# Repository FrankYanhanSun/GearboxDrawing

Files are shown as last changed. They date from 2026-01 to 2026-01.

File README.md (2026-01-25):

# 机械设计课程作业-减速箱

本仓库提供一个开源的机械设计课程作业可供参考。适用于全国广大高等院校机械专业的机械设计课程。需注意：**本仓库设计内容为二级展开式齿轮减速器（斜齿）**，传动简图：

<div align="center">
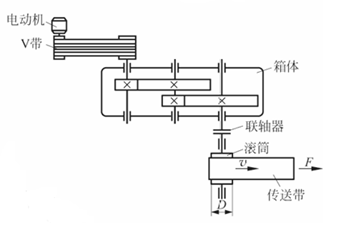
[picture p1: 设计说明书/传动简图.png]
    
</div>

## 初始参数

<div align="center">

| 运输带工作拉力 $F$ | 运输带工作速度 $v$ | 滚筒直径 $D$ | 滚筒效率 $\eta_w$ | 
| --- | --- | --- | --- |
| 5250N | 0.85m/s | 410mm | 0.96 |

</div>

- 两班制，连续单向运转，载荷平稳；要求传动使用寿命为 10 年。

---

## 设计说明书

请见`设计说明书`文件夹，可直接导入`overleaf`进行编辑，需将`Latex`   编译器更改为`XeLaTeX`进行编译。

---

## 图纸

`装配图.dwg`：
<div align="center">
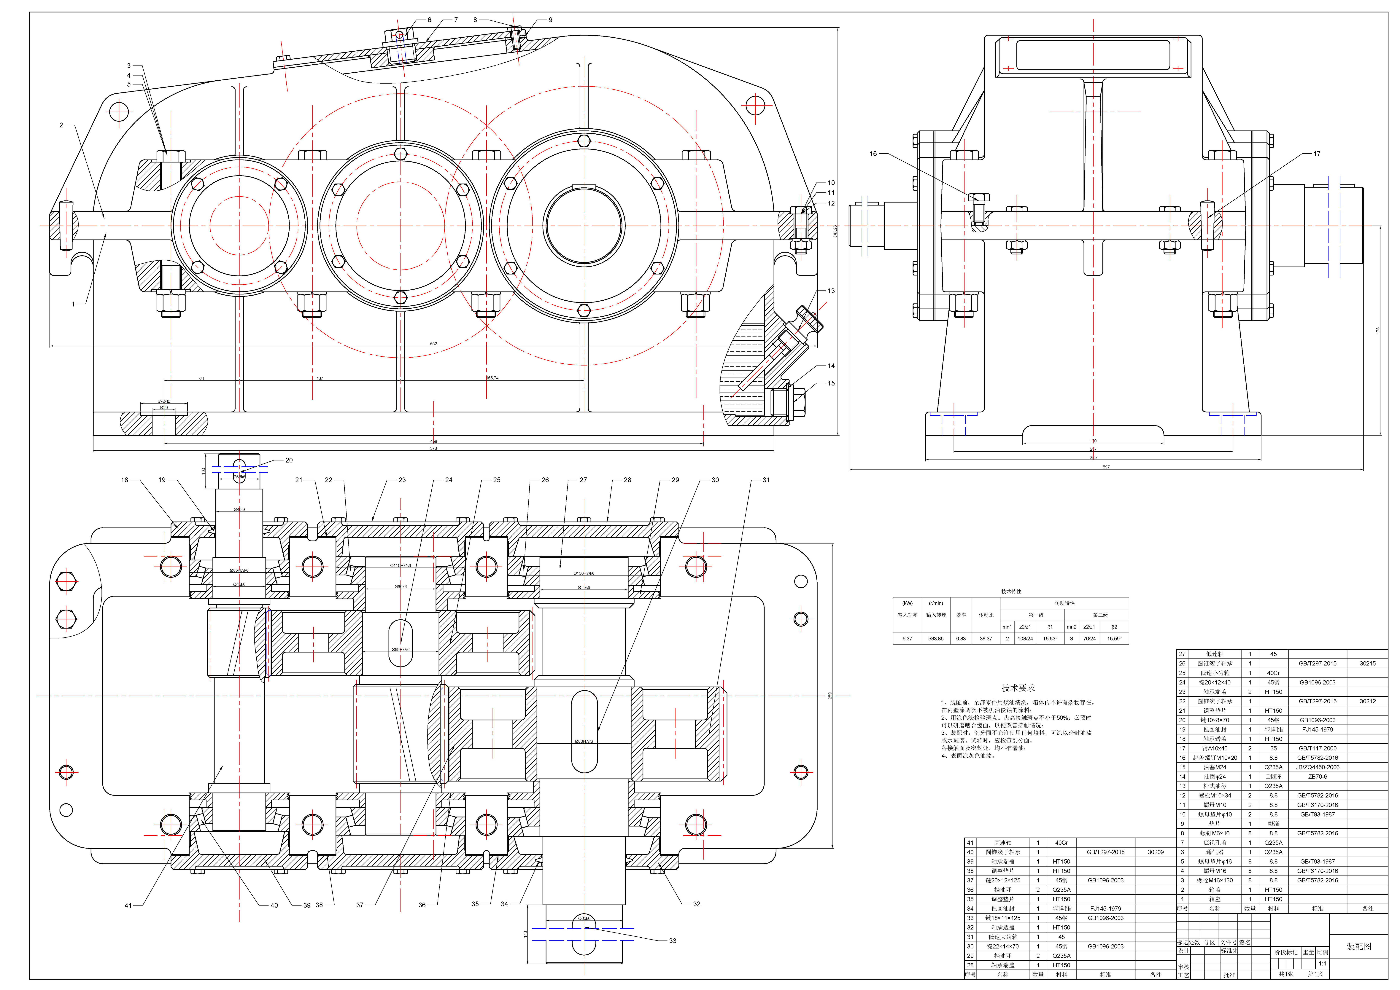
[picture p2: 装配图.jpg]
    
</div>

`零件图(中间轴).dwg`：
<div align="center">
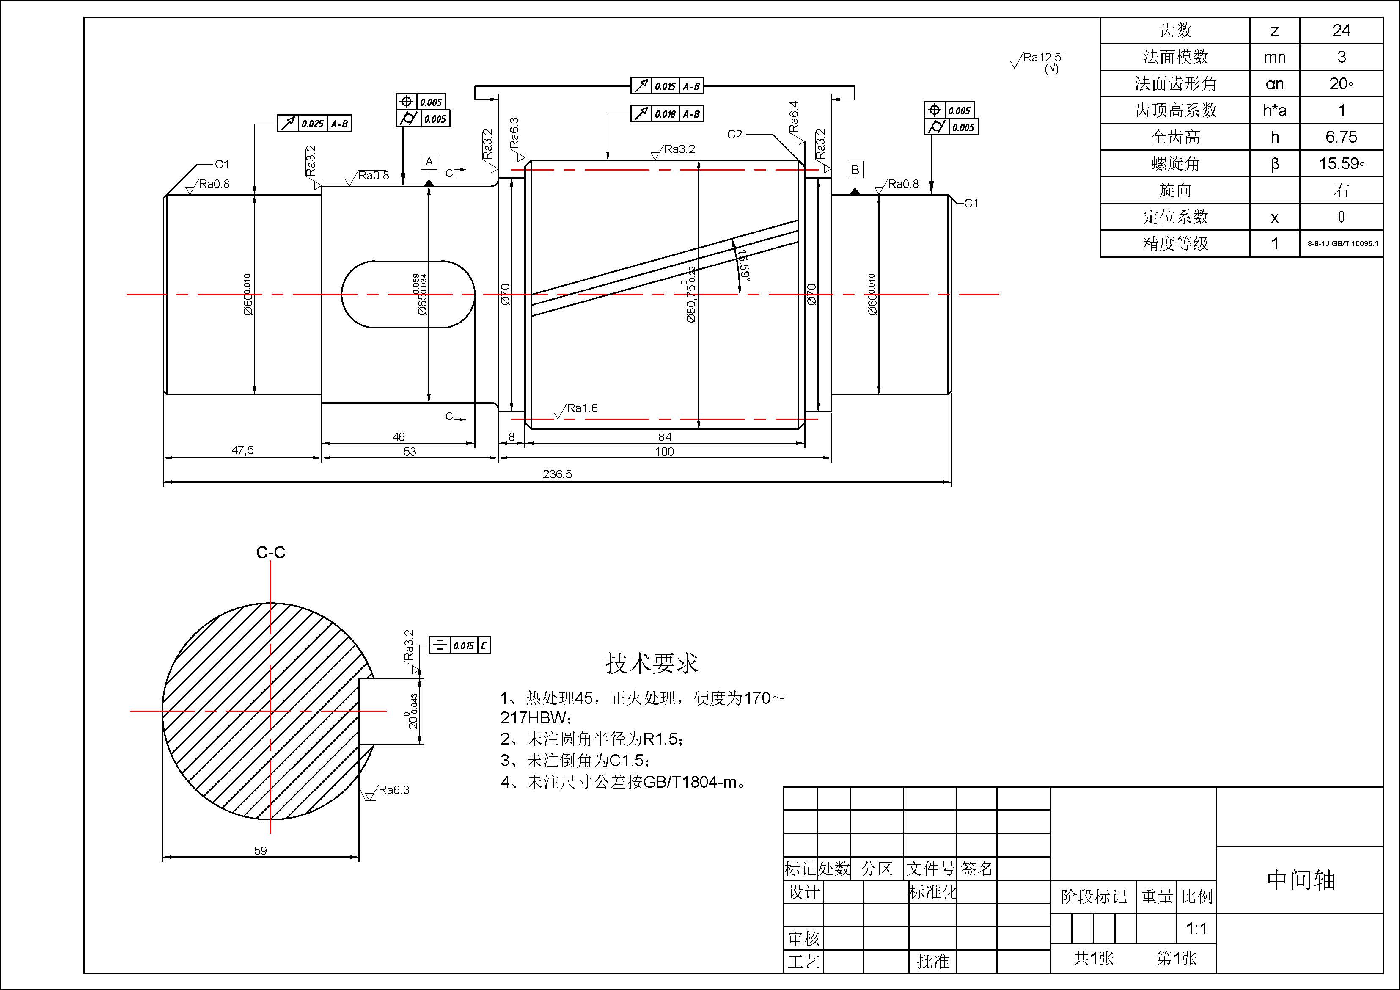
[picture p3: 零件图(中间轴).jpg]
    
</div>

---

## Acknowledgement

感谢b站up主天上一白的视频[机械设计课程设计/减速器设计—全流程详解](https://www.bilibili.com/video/BV1A44y197Hb/?vd_source=a416fcb6c88258170a1902d8753f0269)，帮助我完成了学校老师什么也没讲就布置的作业。看到本仓库的同学也可以去跟着学习一下。

参考书目：
- [《机械设计教程——理论、方法与标准（第2版）》-清华大学出版社](https://detail.tmall.com/item.htm?id=743610688816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)<br>巨烂，计算部分全是错的，但是是我们学校老师编的教材，不得不用
- [《机械设计课程设计（第6版）》-机械工业出版社](https://item.taobao.com/item.htm?id=691022636697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)<br>推荐将本书作为课程设计的参考，流程、标准都很详细

---

$^*$ 所有内容仅供参考，部分内容有错请详细辨认。

---

## Leave a star if you like it 🥰

<br>Star History Chart (https://www.star-history.com/#FrankYanhanSun/GearboxDrawing&Date)
<br>

© 2025 Yanhan Sun (Frank).

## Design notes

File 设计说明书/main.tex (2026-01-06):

\documentclass{article}
\usepackage{geometry}

\geometry{letterpaper,left=2cm,right=2cm,top=3cm,bottom=2cm}
\usepackage{ctex}
\usepackage[english]{babel}
% \usepackage[english]{babel}
\usepackage{amsthm}
\usepackage{amssymb}
\newtheorem{theorem}{Theorem}
\newtheorem{corollary}{Corollary}
\newtheorem{lemma}{Lemma}
\usepackage{amsmath}
\usepackage{graphicx}
\usepackage{multirow}
\usepackage{ulem}
\usepackage{setspace}
\newcommand{\ulinecontent}[2]{\underline{\makebox[#1][c]{#2}}}

\begin{document}
\renewcommand\qedsymbol{$\blacksquare$}

\begin{titlepage}
    \centering
    \onehalfspacing % 1.5倍行距

    % ----------------------------------------------------
    % 顶部：学校名称
    % ----------------------------------------------------
    \vspace*{0.5cm}
    
    % 使用 \zihao{1} 设置一号字 (约26pt)
    % 这里的 \cdot 是中间的点，也可以直接用中文输入法打出
    {\zihao{1} \heiti * \ \ * \ \ 大 \ \ 学}
    
    \vspace{2cm}

    % ----------------------------------------------------
    % 标题：机械设计项目计算说明书
    % ----------------------------------------------------
    % 使用 \zihao{-0} 设置小初号字 (约36pt)
    {\zihao{-0} \heiti 机械设计项目计算说明书}

    \vspace{3cm}

    % ----------------------------------------------------
    % 中间信息栏
    % ----------------------------------------------------
    % 使用表格来对齐标签和下划线
    % l 为左对齐(或居中)，r 为右对齐
    
    {\zihao{3} \songti % 设置字号为三号
        \renewcommand{\arraystretch}{2.0} % 增加表格行高
        
        \begin{tabular}{r @{：} l}
            % \makebox[4.5em][s]{...} 用于强制文字两端对齐(分散对齐)
            
            \textbf{题目 (中文)} & \ulinecontent{260pt}{二级展开式齿轮减速器结构设计} \\
            
            \textbf{\makebox[4.5em][s]{姓名}} & \ulinecontent{260pt}{***} \\
            
            \textbf{\makebox[4.5em][s]{学号}} & \ulinecontent{260pt}{***} \\
            
            \textbf{院 \quad (系)} & \ulinecontent{260pt}{***} \\
            
            \textbf{\makebox[4.5em][s]{专业}} & \ulinecontent{260pt}{***} \\
            
            \textbf{指导教师} & \ulinecontent{260pt}{***} \\
        \end{tabular}
    }

    \vfill % 自动填充垂直空间，把日期推到底部

    % ----------------------------------------------------
    % 底部：日期
    % ----------------------------------------------------
    {\zihao{3} \songti 二〇**年 * 月}
    
    \vspace{2cm}

\end{titlepage}

\newpage
\tableofcontents

\newpage
\section{传动方案}
\subsection{已确定方案：设计带式运输机的展开式二级圆柱齿轮减速器}

\subsection{传动简图}
\begin{figure}[h!]
    \centering
    
    \caption{带式运输机的展开式二级圆柱齿轮减速器的传动简图}
    \label{fig:传动简图}
\end{figure}

\subsection{已知}

（1）运输带工作拉力$F = 5250 \text{N}$；

（2）运输带工作速度 $v = 0.85 \text{m/s}$ (运输带速度允许误差$±5\%$)；

（3）滚筒直径$D = 410 \text{mm}$；

（4）滚筒效率$\eta_w = 0.96$（包括滚筒与轴承的效率损失）；

（5）工作情况: 两班制，连续单向运转，载荷平稳；

（6）要求传动使用寿命为10年。

%提示：请参考“机械设计教程”第1章1.4节，需给出电动机主要参数表、电动机安装及有关尺寸主要参数表、各轴的运动和动力参数表。

\section{电动机的选择}
\subsection{确定电动机功率}
工作主轴所需功率 $P_w$：
\begin{equation}
    P_w = \frac{Fv}{1000} = P_w = \frac{5250 \times 0.85}{1000} = 4.46 \text{kW}
\end{equation}

图片\ref{fig:传动简图}中传动装置包括：V带、三对滚动轴承、两对圆柱齿轮、一个联轴器，总效率为 $\eta = \eta_{\text{V带}} \times \eta_{\text{滚动轴承}}^3 \times \eta_{\text{圆柱齿轮}}^2 \times \eta_{\text{联轴器}} \times \eta_w$。根据表1.3，$\eta_{\text{V带}} = 0.95, \eta_{\text{滚动轴承}} = 0.98, \eta_{\text{圆柱齿轮}} = 0.98, \eta_{\text{联轴器}} = 0.99$。可以得到：
\begin{equation}
    \eta = \eta_{\text{V带}} \times \eta_{\text{滚动轴承}}^3 \times \eta_{\text{圆柱齿轮}}^2 \times \eta_{\text{联轴器}} \times \eta_w = 0.95 \times 0.98^3 \times 0.98^2 \times 0.99 \times 0.96 = 0.83
\end{equation}

电动机所需功率$P_d$:
\begin{equation}
    P_d = \frac{P_w}{\eta} = \frac{4.46}{0.83} = 5.37 \text{kW}
\end{equation}

考虑到在各零部件设计时需要有一定的工况系数，取电动机的工况系数为1.3，则电动机的额定功率$P_{ed}$：
\begin{equation}
    P_{ed} \ge  k_A P_d = 1.3 \times 5.37 = 6.98 \text{kW}
\end{equation}
根据附表K.1，选取电动机额定功率$P_{ed} = 7.5 \text{kW}$

\subsection{确定电动机转速}
工作机主轴转速 $n_w$：
\begin{equation}
    n_w = \frac{60 \times 1000 \times v}{\pi D} = \frac{60 \times 1000 \times 0.85}{\pi \times 410} = 39.59 \text{r/min}
\end{equation}

根据工作机主轴转速 $n_w$ 及有关机械传动的常用传动比范围(见表 1.2), 取普通 V 带的传动比 $i_带 = 2\textasciitilde{}4$, 二级圆柱齿轮传动比 $i_1 = i_2 = 3\textasciitilde{}6$, 可计算电动机转速的合理范围为 $n_d = n_w i_1 i_2 i_3 = 39.59 \times (2\textasciitilde{}4) \times (3\textasciitilde{}6) \times (3\textasciitilde{}6) \text{r/min} = 712.62\textasciitilde{}5700.96 \text{r/min}$。

根据附表 K.1, 符合这一范围的电动机同步转速有 $750 \text{r/min}$、1000 \text{r/min}$、1500 \text{r/min}$ 和 $3000 \text{r/min}$ 4 种, 现选用同步转速 $1500 \text{r/min}$, 满载转速 $n_m = 1440 \text{ r/min}$ 的电动机, 查得其主要参数和安装尺寸如表\ref{tab:电动机主要参数}和表\ref{tab:电动机安装及有关尺寸主要参数}所示。

\begin{table}[h]
\centering
\caption{电动机主要参数}
\label{tab:电动机主要参数}
\begin{tabular}{|c|c|c|c|c|c|}
\hline
型号 & 额定功率 & 同步转速 & 满载转速 & 堵转转矩/额定转矩 & 最大转矩/额定转矩 \\
\hline
Y132M-4 & 7.5kW & 1500r/min & 1440r/min & 2.2 & 2.2 \\
\hline
\end{tabular}
\end{table}

\begin{table}[h]
\centering
\caption{电动机安装及有关尺寸主要参数 \ \ mm}
\label{tab:电动机安装及有关尺寸主要参数}
\begin{tabular}{|c|c|c|c|c|c|}
\hline
\multirow{2}{*}{中心高} & 外形尺寸 & 地脚安装 & 地脚螺栓 & 轴伸尺寸 & 键公称尺寸 \\
 & $L \times (AC/2 + AD) \times HD$ & 尺寸 $A \times B$ & 直径 $K$ & $D \times E$ & $F \times h$ \\
\hline
132 & $515 \times 345 \times 315$ & $216 \times 178$ & 12 & $38 \times 80$ & $10 \times 8$ \\
\hline
\end{tabular}
\end{table}

\subsection{传动装置总传动比的计算及各级传动比的分配}
传动装置总传动比$i$:
\begin{equation}
    i = \frac{n_m}{n_w} = \frac{1440}{39.59} = 36.37
\end{equation}
取$i_{\text{V带}} = 2.6$， 那么$i_1 i_2 = i / i_{\text{V带}} = 13.98$，查表1.7得：一级齿轮传动比$i_1 = 4.5$，二级齿轮传动比$i_2 = 3.15$，误差为$e = |3.15 \times 4.5 \times 2.6 - 36.37| / 36.37 = 1.3\% $，误差控制在$±(3\textasciitilde{}5)\%$以内。

\subsection{传动装置运动和动力参数计算}

\subsubsection{计算各轴输入功率}
v带轴功率 $P_d = 5.37 \text{ kW}$

齿轮轴I功率 $P_I = P_d \eta_{\text{v带}} = 5.37 \times 0.95 \text{ kW} = 5.10 \text{ kW}$

齿轮轴II功率 $P_{II} = P_I \eta_{\text{滚动轴承}} \eta_{\text{圆柱齿轮}} = 5.10 \times 0.98^2 \text{ kW} = 4.90 \text{ kW}$

齿轮轴III功率 $P_{III} = P_{II} \eta_{\text{滚动轴承}} \eta_{\text{圆柱齿轮}} = 4.90 \times 0.98^2 \text{ kW} = 4.71 \text{ kW}$

\subsubsection{计算各轴转速}
v带轴转速 $n_d = n_m = 1440 \text{ r/min}$

齿轮轴I转速 $n_I = \frac{n_d}{i_{\text{v带}}} = \frac{1440}{2.6} = 553.85 \text{ r/min}$

齿轮轴II转速 $n_{II} = \frac{n_I}{i_1} = \frac{553.85}{4.5} = 123.08 \text{ r/min}$

齿轮轴III转速 $n_{III} = \frac{n_{II}}{i_2} = \frac{123.08}{3.15} = 39.07 \text{ r/min}$

\subsubsection{计算各轴转矩}
v带轴转矩 $T_d = 9550\frac{P_d}{n_d} = 9550 \times \frac{5.37}{1440} = 35.61 \text{ N} \cdot \text{m}$

齿轮轴I转矩 $T_I = 9550\frac{P_I}{n_I} = 9550 \times \frac{5.1015}{553.85} = 87.97 \text{ N} \cdot \text{m}$

齿轮轴II转矩 $T_{II} = 9550\frac{P_{II}}{n_{II}} = 9550 \times \frac{4.8995}{123.08} = 380.17 \text{ N} \cdot \text{m}$

齿轮轴III转矩 $T_{III} = 9550\frac{P_{III}}{n_{III}} = 9550 \times \frac{4.7055}{39.07} = 1150.14 \text{ N} \cdot \text{m}$

\section{带传动设计}

\subsection{已知}
（1）电动机功率$P=5.37kW$

（2）电动机转速$n_{1}=1440r/min$

（3）减速箱高速轴转速$n_{2}=553.85r/min$

\subsection{功率计算}
根据载荷性质和每天运转时间, 根据表5.6确定工作情况系数 $K_{A}=1.2$
\begin{equation}
P_{ca}=K_{A}P_{d}=1.2\times5.37=6.44(kW)
\end{equation}

\subsection{带型选择}
根据 $P_{ca}$ 与 $n_{d}$, 由图5.8确定选用B型普通V带。

\subsection{确定带轮基准直径}
由表5.2取小带轮基准直径 $D_{1}=132mm$。 根据式(5.24), 计算从动轮基准直径 $D_{2}$
\begin{equation}
D_{2}=iD_{1}=2.6\times132=343.2(mm)
\end{equation}
根据表5.4, 取 $D_{2}=355~mm$。
按式(5.23)验算带的速度
\begin{equation}
v=\frac{\pi D_{1}n_{1}}{60\times1000}=\frac{\pi\times132\times1440}{60\times1000}=9.95(m/s)<30(m/s)
\end{equation}
带的速度合适。

\subsection{确定V带的基准长度和传动中心距}
根据 $0.7(D_{1}+D_{2})<a_0<2(D_{1}+D_{2})$, 初选中心距 $a_{0}=600mm$。 根据式(5.25), 带长约为 $L_{d}^{\prime}=
a_{0}+\frac{\pi}{2}(D_{1}+D_{2})+\frac{(D_{2}-D_{1})^{2}}{4a_{0}}=1985.7mm$。

由表5.3选带的基准长度 $L_{d}=2000mm$。 按式(5.26)计算实际中心距a为
\begin{equation}
a=a_{0}+\frac{L_{d}-L_{d}^{\prime}}{2}=607.15mm
\end{equation}

\subsection{验算主动轮上的包角 $\alpha_{1}$}
由式(5.29)得
\begin{equation}
\alpha_{1}=180^{\circ}-\frac{D_{2}-D_{1}}{a}\times60^{\circ}=180^{\circ}-\frac{355-132}{607.15}\times60^{\circ}=157.96^{\circ}>120^{\circ}
\end{equation}
小带轮上包角合适。

\subsection{计算V带的根数z}
由 $n_{1}=1440r/min$, $D_{1}=132mm$, $i=2.6$, 查表5.7(a)和表5.7(b)得 $P_{0}=2.5kW$, $\Delta P_{0}=0.46kW$, 查表5.8得 $K_{\alpha}=0.95$, 查表5.9得 $K_{L}=0.98$, 则由式(5.30)得
\begin{equation}
z=\frac{P_{ca}}{(P_{0}+\Delta P_{0})K_{\alpha}K_{L}}=\frac{6.44}{(2.5+0.46)\times0.95\times0.98}=2.3
\end{equation}
取 $z=3$ 根。

\subsection{计算预紧力 $F_{0}$}
查表5.1得 $q=0.17kg/m$, 由式(5.32)得
\begin{equation}
F_{0}=500\frac{P_{ca}}{vz}(\frac{2.5}{K_{\alpha}}-1)+qv^{2}=500 \times \frac{6.44}{9.95 \times 3}(\frac{2.5}{0.95}-1)+0.17\times9.95^{2} = 192.83(N)
\end{equation}

\subsection{计算作用在轴上的压轴力 $F_{Q}$}
由式(5.33)得
\begin{equation}
F_{Q}=2z F_{0} \sin\frac{\alpha_{1}}{2}=2\times3\times192.83 \times \sin\frac{157.96^{\circ}}{2}=1135.65(N)
\end{equation}

\subsection{其他}
V带轮采用HT200制造, 允许最大圆周速度为 $25~m/s$。

\section{齿轮设计}

\subsection{高速齿轮设计}
\subsubsection{选择齿轮类型、材料、精度及参数}
(1)大小齿轮都选用硬齿面。 选大、小齿轮的材料均为45钢,并经调质后表面淬火,齿面硬度均为45HRC。

(2)选取等级精度。初选7级精度 (GB/T T10095.1-2022)。

(3)选小齿轮齿数 $z_{1}=24$, 大齿轮齿数 $z_{2} = i_1 z_1 =  4.5 \times 24 = 108$, 取 $z_{2}=108$。

(4)初选螺旋角 $\beta=15^{\circ}$。

\subsubsection{按齿面接触疲劳强度设计}
按齿面接触疲劳强度设计
考虑到闭式硬齿面齿轮传动失效形式可能是点蚀,也可能为疲劳折断,故按接触疲劳强度设计后,按齿根弯曲强度校核 。

按设计计算公式(7.28)进行试算,有
\begin{equation}d_{1}=\sqrt[3]{\frac{2KT_{1}}{\phi_{d}\epsilon_{a}}\cdot\frac{i\pm1}{i}(\frac{Z_{H}Z_{E}}{[\sigma_{H}]})^{2}} \end{equation}

下面确定公式内的各计算数值 。

(1)载荷系数K: 试选 $K=1.5$ 。

(2)小齿轮传递的转矩: $T_{1}=87.97N \cdot m=87970N \cdot mm$ 。

(3)齿宽系数 $\phi_{d}$: 由表7.7选取 $\phi_{d}=1$ 。

(4)弹性影响系数 $Z_{E}$: 由表7.8查得 $Z_{E}=189.8MPa^{1/2}$ 。

(5)节点区域系数 $Z_{H}$: 因为 $Z_{H}=\sqrt{\frac{2\cos\beta_{b}}{\sin\alpha_{t}\cos\alpha_{t}}}$ ，由$\tan\alpha_{t}=\frac{\tan\alpha_{n}}{\cos\beta}$ 和 $\tan\beta_{b}=\tan\beta\cos\alpha_{t}$ 得:

\begin{equation}a_{t}=\arctan(\frac{\tan a_{n}}{\cos\beta})=\arctan(\frac{\tan 20^{\circ}}{\cos 15^{\circ}})=20.65^{\circ} \end{equation}

\begin{equation}\beta_{b}=\arctan(\tan\beta \cos a_{t})=\arctan(\tan 15^{\circ} \cos 20.65^{\circ})=14.08^{\circ} \end{equation}

\begin{equation}Z_{H}=\sqrt{\frac{2 \cos 14.08^{\circ}}{\sin 20.65^{\circ} \cos 20.65^{\circ}}}=2.425 \end{equation}

(6)按《机械原理》给出端面重合度 $\epsilon_{a}$ :

\begin{equation}\epsilon_{a}=\frac{z_{1}(\tan a_{at1}-\tan a_{t})+z_{2}(\tan a_{at2}-\tan a_{t})}{2\pi} \end{equation}

\begin{equation}a_{at1}=\arccos(\frac{z_{1}\cos a_{t}}{z_{1}+2h_{an}^{*}\cos\beta})=\arccos(\frac{24\times \cos 20.65^{\circ}}{24+2\times 1\times \cos 15^{\circ}})=30.00^{\circ} \end{equation}

\begin{equation}a_{at2}=\arccos(\frac{z_{2}\cos a_{t}}{z_{2}+2h_{an}^{*}\cos\beta})=\arccos(\frac{108\times \cos 20.65^{\circ}}{108+2\times 1\times \cos 15^{\circ}})=23.18^{\circ} \end{equation}

代入上式得

\begin{equation}\epsilon_{a}=\frac{24\times(\tan 30.00^{\circ}-\tan 20.65^{\circ})+108\times(\tan 23.18^{\circ}-\tan 20.65^{\circ})}{2\pi}=1.650 \end{equation}

(7)接触疲劳强度极限 $\sigma_{Hlim}$: 由表7.3按齿面硬度查得 $\sigma_{Hlim1}=\sigma_{Hlim2}=1000MPa$ 。

(8)应力循环次数:

\begin{equation}N_{1}=60n_{1}jL_{h}=60\times 553.85\times 1\times(2\times 8\times 300\times 10)=1.6\times 10^{9} \end{equation}

\begin{equation}N_{2}=\frac{N_{1}}{i_{2}}=\frac{1.6\times 10^{9}}{4.5}=3.556\times 10^{8} \end{equation}

(9)接触疲劳寿命系数 $K_{HN}$: 由图7.3查得 $K_{HN1}=0.9$, $K_{HN2}=0.95$ 。

(10)接触疲劳许用应力 $[\sigma_{H}]$: 取失效概率为1\%, 安全系数$S_H=1$

\begin{equation}[\sigma_{H}]_{1}=K_{HN1}\sigma_{Hlim1}/S_{H}=0.9\times 1000/1=900MPa \end{equation}

\begin{equation}[\sigma_{H}]_{2}=K_{HN2}\sigma_{Hlim2}/S_{H}=0.95\times 1000/1=950MPa \end{equation}

故取 $[\sigma_{H}]= \frac{[\sigma_{H}]_{1} + [\sigma_{H}]_{2}}{2} = 925MPa$ 。

\subsubsection{计算}
(1)计算小齿轮分度圆直径 $d_{1t}$ 。

\begin{equation}d_{1t} \ge \sqrt[3]{\frac{2K_{t}T_{1}}{\phi_{d}\epsilon_{a}}\cdot\frac{i+1}{i}(\frac{Z_{H}Z_{E}}{[\sigma_{H}]})^{2}}=\sqrt[3]{\frac{2\times 1.5\times 87970}{1\times 1.650}\times\frac{4.5+1}{4.5}\times(\frac{2.425\times 189.8}{925})^{2}}=42.76 mm \end{equation}

(2)计算圆周速度 $v$ :

\begin{equation}v=\frac{\pi d_{1t}n_{1}}{60\times 1000}=\frac{\pi\times 42.76\times 553.85}{60000}=1.24 m/s \end{equation}

(3)计算齿宽 $b$ :

\begin{equation}b=\phi_{d}d_{1t}=1\times 42.76=42.76 mm \end{equation}

(4)计算齿宽与齿高之比 $b/h$ 。

\begin{equation}b/h = \phi_{d}d_{1t}/(2.25m_{n}) = \phi_{d}(m_{n}z_{1}/\cos\beta)/(2.25m_{n}) = \phi_{d}z_{1}/(2.25\cos\beta) = 1\times 24/(2.25\times \cos 15^{\circ})=11.02 \end{equation}

(5)计算载荷系数 $K$ :

根据 $v=1.24 m/s$, 7级精度, 由图7.5查得动载系数 $K_{v}=1.04$; 由表7.5查得 $K_{a}=1.2$; 由表7.4 查得使用系数 $K_{A}=1$; 由表7.6查得 $K_{H\beta}=1.0 + 0.31(1 + 0.6\phi^2_d)\phi^2_d+0.19\times10^{-3}b = 1.50$; 由图7.6查得齿向载荷分布系数$K_{F\beta} = 1.48$; 载荷系数为

\begin{equation}K=K_{A}K_{v}K_{a}K_{H\beta}=1.0\times 1.04\times 1.2\times 1.50=1.872 \end{equation}

(6)按实际的载荷系数修正分度圆直径 。

\begin{equation}d_{1}=d_{1t}\sqrt[3]{\frac{K}{K_{t}}}=42.76\times\sqrt[3]{\frac{1.872}{1.5}}=46.04 mm \end{equation}

(7)计算模数 $m_{n}$ 。

\begin{equation}m_{n}=\frac{d_{1}\cos\beta}{z_{1}}=\frac{46.04\times \cos 15^{\circ}}{24}=1.853 mm \end{equation}

按表7.10取 $m_{n}=2mm$ 。

\subsubsection{按齿根弯曲疲劳强度校核}
校核公式为(7.29) :

\begin{equation}\sigma_{F}=\frac{2KT_{1}Y_{\beta}\cos^{2}\beta}{\phi_{d}\epsilon_{a}z_{1}^{2}m_{n}^{3}}Y_{Fa}Y_{Sa}\le[\sigma_{F}] \end{equation}

公式中的各参数确定如下 。

(1)载荷系数 $K$ :

前面已查得 $K_{A}=1$, $K_{v}=1.04$, $K_{a}=1.2$, $K_{F\beta}=1.48$, 则有

\begin{equation}K=K_{A}K_{v}K_{a}K_{F\beta}=1\times 1.04\times 1.2\times 1.48=1.85 \end{equation}

(2)齿形系数 $Y_{Fa}$ 和应力校正系数 $Y_{Sa}$ :

小齿轮当量齿数 $z_{v1}=z_{1}/\cos^{3}\beta=\frac{24}{\cos^{3}15^{\circ}}=\frac{24}{0.9012}=26.63$，大齿轮当量齿数 $z_{v2}=z_{2}/\cos^{3}\beta=\frac{108}{\cos^{3}15^{\circ}}=\frac{108}{0.9012}=119.84$

查表 7.9, $Y_{Fa1}=2.57$, $Y_{Sa1}=1.60$, $Y_{Fa2}=2.18$, $Y_{Sa2}=1.79$ 。

(3)螺旋角影响系数 $Y_{\beta}$ :

轴面重合度 $\epsilon_{\beta}=0.318\phi_{d}z_{1}\tan\beta=0.318\times 1\times 24\times \tan 15^{\circ}=2.045$，取 $\epsilon_{\beta}=1$, 则

\begin{equation}Y_{\beta}=1-\epsilon_{\beta}\times\frac{\beta}{120^{\circ}}=1-1\times\frac{15}{120}=0.875 \end{equation}

(4)许用弯曲应力 $[\sigma_{F}]$ :

查图7.4得 $K_{FN1}=0.85$, $K_{FN2}=0.87$;

查表7.2得 $\sigma_{Flim1}=500MPa$, $\sigma_{Flim2}=500MPa$ 。

取安全系数 $S_{F}=1.4,$ 则

\begin{equation}[\sigma_{F}]_{1}=K_{FN1}\sigma_{Flim1}/S_{F}=0.85\times 500/1.4=304MPa \end{equation}

\begin{equation}[\sigma_{F}]_{2}=K_{FN2}\sigma_{Flim2}/S_{F}=0.87\times 500/1.4=311MPa \end{equation}

(5)校核:

小齿轮

\begin{equation} \begin{aligned} \sigma_{F1} &= \frac{2KT_{1}Y_{\beta}\cos^{2}\beta}{\phi_{d}\epsilon_{a}z_{1}^{2}m_{n}^{3}}Y_{Fa1}Y_{Sa1} \\ &= \frac{2\times 1.85\times 87970\times 0.875\times \cos^{2}\beta}{1\times 1.65\times 24^{2}\times 2^{3}}\times 2.57\times 1.60=143.71 \le [\sigma_{F}]_{1} \end{aligned} \end{equation}

大齿轮

\begin{equation} \begin{aligned} \sigma_{F2} &= \frac{2KT_{2}Y_{\beta}\cos^{2}\beta}{\phi_{d}\epsilon_{a}z_{2}^{2}m_{n}^{3}}Y_{Fa2}Y_{Sa2} \\ &= \frac{2\times 1.85\times 380170\times 0.875\times \cos^{2}\beta}{1\times 1.65\times 108^{2}\times 2^{3}}\times 2.18\times 1.79=27.64 \le [\sigma_{F}]_{2} \end{aligned} \end{equation}

大小齿轮齿根弯曲疲劳强度均满足 。

由上述结果可见齿轮传动的弯曲强度有相当大的余量，故通常是按接触强度设计，确定方案后，需弯曲强度校核，这样计算比较简单。也可分别按两种强度设计，分析对比，确定方案，这样有时可以得到较优的解。

\subsubsection{齿轮传动几何尺寸计算}
(1)中心距: $a=m_{n}(z_{1}+z_{2})/(2\cos\beta)=2\times(24+108)/(2\cos 15^{\circ})=136.7mm$。 取 $a=137mm$ 。

(2)修正螺旋角: $\beta=\arccos[m_{n}(z_{1}+z_{2})/(2a)]=\arccos[2\times(24+108)/(2\times 137)]=15.53^{\circ}$ 。

(3)分度圆直径 :

\begin{equation}d_{1}=m_{n}z_{1}/\cos\beta=2\times 24/\cos 15.53^{\circ}=49.82mm \end{equation}

\begin{equation}d_{2}=m_{n}z_{2}/\cos\beta=2\times 108/\cos 15.53^{\circ}=224.18mm \end{equation}

(4)齿宽 :

\begin{equation}b=\phi_{d}d_{1}=1\times 49.82=49.82mm \end{equation}
取 $B_{2}=50mm$, $B_{1}=B_{2}+5=55mm$ 。

具体设计参数如表所示 。

\subsubsection{结果}
\begin{table}[h]
\centering
\caption{高速级齿轮}
\label{tab:gear_parameters1}
\begin{tabular}{|l|l|l|}
\hline
名称 & 代 号 & 计算公式与结果 \\ \hline
法向模数 & $m_{n}$ & 2mm \\ \hline
端面模数 & $m_{t}$ & $m_{t}=\frac{m_{n}}{\cos\beta}=2.08mm$ \\ \hline
螺旋角 & $\beta$ & $15.53^{\circ}$ \\ \hline
法向压力角 & $\alpha_{n}$ & $20^{\circ}$ \\ \hline
端面压力角 & $\alpha_{t}$ & $\alpha_{t}=\arctan(\frac{\tan\alpha_{n}}{\cos\beta})=20.70^{\circ}$ \\ \hline
分度圆直径 & $d_{1}, d_{2}$ & $49.82mm, 224.18mm$ \\ \hline
齿顶高 & $h_{a}$ & 2mm \\ \hline
齿根高 & $h_{f}$ & 2.5mm \\ \hline
全齿高 & $h$ & 4.5mm \\ \hline
顶隙 & $c$ & 0.5mm \\ \hline
齿顶圆直径 & $d_{a1}, d_{a2}$ & $53.82mm, 228.18mm$ \\ \hline
齿根圆直径 & $d_{f1}, d_{f2}$ & $44.82mm, 219.18mm$ \\ \hline
中心距 & $a$ & 137mm \\ \hline
传动比 & $i$ & 4.5 \\ \hline
齿数 & $z_{1}, z_{2}$ & 24, 108 \\ \hline
齿宽 & $b_{1}, b_{2}$ & 55mm, 50mm \\ \hline
螺旋方向 & & 小齿轮右旋, 大齿轮左旋 \\ \hline
大齿轮轮毂宽 & $B_{2}$ & 55mm \\ \hline
\end{tabular}
\end{table}

\subsection{低速齿轮设计}
\subsubsection{选择齿轮类型、材料、精度及参数}
(1)大小齿轮都选用硬齿面。 选大、小齿轮的材料均为45钢,并经调质后表面淬火,齿面硬度均为45HRC。

(2)选取等级精度。初选7级精度 (GB/T T10095.1-2022)。

(3)选小齿轮齿数 $z_{1}=24$, 大齿轮齿数 $z_{2} = i_2 z_1 =  3.15 \times 24 = 75.6$, 取 $z_{2}=76$。

(4)初选螺旋角 $\beta=15^{\circ}$。

\subsubsection{按齿面接触疲劳强度设计}
按齿面接触疲劳强度设计
考虑到闭式硬齿面齿轮传动失效形式可能是点蚀,也可能为疲劳折断,故按接触疲劳强度设计后,按齿根弯曲强度校核 。

按设计计算公式(7.28)进行试算,有
\begin{equation}d_{1}=\sqrt[3]{\frac{2KT_{1}}{\phi_{d}\epsilon_{a}}\cdot\frac{i\pm1}{i}(\frac{Z_{H}Z_{E}}{[\sigma_{H}]})^{2}} \end{equation}

下面确定公式内的各计算数值 。

(1)载荷系数K: 试选 $K=1.5$ 。

(2)小齿轮传递的转矩: $T_{2}=380.17N \cdot m=380170N \cdot mm$ 。

(3)齿宽系数 $\phi_{d}$: 由表7.7选取 $\phi_{d}=1$ 。

(4)弹性影响系数 $Z_{E}$: 由表7.8查得 $Z_{E}=189.8MPa^{1/2}$ 。

(5)节点区域系数 $Z_{H}$: 因为 $Z_{H}=\sqrt{\frac{2\cos\beta_{b}}{\sin\alpha_{t}\cos\alpha_{t}}}$ ，由$\tan\alpha_{t}=\frac{\tan\alpha_{n}}{\cos\beta}$ 和 $\tan\beta_{b}=\tan\beta\cos\alpha_{t}$ 得:

\begin{equation}a_{t}=\arctan(\frac{\tan a_{n}}{\cos\beta})=\arctan(\frac{\tan 20^{\circ}}{\cos 15^{\circ}})=20.65^{\circ} \end{equation}

\begin{equation}\beta_{b}=\arctan(\tan\beta \cos a_{t})=\arctan(\tan 15^{\circ} \cos 20.65^{\circ})=14.08^{\circ} \end{equation}

\begin{equation}Z_{H}=\sqrt{\frac{2 \cos 14.08^{\circ}}{\sin 20.65^{\circ} \cos 20.65^{\circ}}}=2.425 \end{equation}

(6)按《机械原理》给出端面重合度 $\epsilon_{a}$ :

\begin{equation}\epsilon_{a}=\frac{z_{1}(\tan a_{at1}-\tan a_{t})+z_{2}(\tan a_{at2}-\tan a_{t})}{2\pi} \end{equation}

\begin{equation}a_{at1}=\arccos(\frac{z_{1}\cos a_{t}}{z_{1}+2h_{an}^{*}\cos\beta})=\arccos(\frac{24\times \cos 20.65^{\circ}}{24+2\times 1\times \cos 15^{\circ}})=30.00^{\circ} \end{equation}

\begin{equation}a_{at2}=\arccos(\frac{z_{2}\cos a_{t}}{z_{2}+2h_{an}^{*}\cos\beta})=\arccos(\frac{76\times \cos 20.65^{\circ}}{76+2\times 1\times \cos 15^{\circ}})=24.14^{\circ} \end{equation}

代入上式得

\begin{equation}\epsilon_{a}=\frac{24\times(\tan 30.00^{\circ}-\tan 20.65^{\circ})+76\times(\tan 24.14^{\circ}-\tan 20.65^{\circ})}{2\pi}=1.63 \end{equation}

(7)接触疲劳强度极限 $\sigma_{Hlim}$: 由表7.3按齿面硬度查得 $\sigma_{Hlim1}=\sigma_{Hlim2}=1000MPa$ 。

(8)应力循环次数:

\begin{equation}N_{1}=60n_{2}jL_{h}=60\times 123.08\times 1\times(2\times 8\times 300\times 10)=3.5\times 10^{8} \end{equation}

\begin{equation}N_{2}=\frac{N_{1}}{i_{2}}=\frac{3.5\times 10^{8}}{3.15}=1.125\times 10^{8} \end{equation}

(9)接触疲劳寿命系数 $K_{HN}$: 由图7.3查得 $K_{HN1}=0.95$, $K_{HN2}=0.97$ 。

(10)接触疲劳许用应力 $[\sigma_{H}]$: 取失效概率为1\%, 安全系数$S_H=1$

\begin{equation}[\sigma_{H}]_{1}=K_{HN1}\sigma_{Hlim1}/S_{H}=0.95\times 1000/1=950MPa \end{equation}

\begin{equation}[\sigma_{H}]_{2}=K_{HN2}\sigma_{Hlim2}/S_{H}=0.97\times 1000/1=970MPa \end{equation}

故取 $[\sigma_{H}]= \frac{[\sigma_{H}]_{1} + [\sigma_{H}]_{2}}{2} = 960MPa$ 。

\subsubsection{计算}
(1)计算小齿轮分度圆直径 $d_{1t}$ 。

\begin{equation}d_{1t} \ge \sqrt[3]{\frac{2K_{t}T_{2}}{\phi_{d}\epsilon_{a}}\cdot\frac{i+1}{i}(\frac{Z_{H}Z_{E}}{[\sigma_{H}]})^{2}}=\sqrt[3]{\frac{2\times 1.5\times 380170}{1\times 1.63}\times\frac{3.15+1}{3.15}\times(\frac{2.425\times 189.8}{960})^{2}}=59.26 mm \end{equation}

(2)计算圆周速度 $v$ :

\begin{equation}v=\frac{\pi d_{1t}n_{2}}{60\times 1000}=\frac{\pi\times 59.26\times 123.08}{60000}=0.382 m/s \end{equation}

(3)计算齿宽 $b$ :

\begin{equation}b=\phi_{d}d_{1t}=1\times 59.26=59.26 mm \end{equation}

(4)计算齿宽与齿高之比 $b/h$ 。

\begin{equation}b/h = \phi_{d}d_{1t}/(2.25m_{n}) = \phi_{d}(m_{n}z_{1}/\cos\beta)/(2.25m_{n}) = \phi_{d}z_{1}/(2.25\cos\beta) = 1\times 24/(2.25\times \cos 15^{\circ})=11.02 \end{equation}

(5)计算载荷系数 $K$ :

根据 $v=0.382 m/s$, 7级精度, 由图7.5查得动载系数 $K_{v}=1.02$; 由表7.5查得 $K_{a}=1.2$; 由表7.4 查得使用系数 $K_{A}=1$; 由表7.6查得 $K_{H\beta}=1.0 + 0.31(1 + 0.6\phi^2_d)\phi^2_d+0.19\times10^{-3}b = 1.51$; 由图7.6查得齿向载荷分布系数$K_{F\beta} = 1.48$; 载荷系数为

\begin{equation}K=K_{A}K_{v}K_{a}K_{H\beta}=1.0\times 1.02\times 1.2\times 1.51=1.848 \end{equation}

(6)按实际的载荷系数修正分度圆直径 。

\begin{equation}d_{1}=d_{1t}\sqrt[3]{\frac{K}{K_{t}}}=59.26\times\sqrt[3]{\frac{1.848}{1.5}}=63.53 mm \end{equation}

(7)计算模数 $m_{n}$ 。

\begin{equation}m_{n}=\frac{d_{1}\cos\beta}{z_{1}}=\frac{63.53\times \cos 15^{\circ}}{24}=2.56 mm \end{equation}

按表7.10取 $m_{n}=3mm$ 。

\subsubsection{按齿根弯曲疲劳强度校核}
校核公式为(7.29) :

\begin{equation}\sigma_{F}=\frac{2KT_{1}Y_{\beta}\cos^{2}\beta}{\phi_{d}\epsilon_{a}z_{1}^{2}m_{n}^{3}}Y_{Fa}Y_{Sa}\le[\sigma_{F}] \end{equation}

公式中的各参数确定如下 。

(1)载荷系数 $K$ :

前面已查得 $K_{A}=1$, $K_{v}=1.02$, $K_{a}=1.2$, $K_{F\beta}=1.51$, 则有

\begin{equation}K=K_{A}K_{v}K_{a}K_{F\beta}=1\times 1.02\times 1.2\times 1.51=1.85 \end{equation}

(2)齿形系数 $Y_{Fa}$ 和应力校正系数 $Y_{Sa}$ :

小齿轮当量齿数 $z_{v1}=z_{1}/\cos^{3}\beta=\frac{24}{\cos^{3}15^{\circ}}=\frac{24}{0.9012}=26.63$，大齿轮当量齿数 $z_{v2}=z_{2}/\cos^{3}\beta=\frac{76}{\cos^{3}15^{\circ}}=\frac{76}{0.9012}=84.33$

查表 7.9, $Y_{Fa1}=2.57$, $Y_{Sa1}=1.60$, $Y_{Fa2}=2.20$, $Y_{Sa2}=1.78$ 。

(3)螺旋角影响系数 $Y_{\beta}$ :

轴面重合度 $\epsilon_{\beta}=0.318\phi_{d}z_{1}\tan\beta=0.318\times 1\times 24\times \tan 15^{\circ}=2.045$，取 $\epsilon_{\beta}=1$, 则

\begin{equation}Y_{\beta}=1-\epsilon_{\beta}\times\frac{\beta}{120^{\circ}}=1-1\times\frac{15}{120}=0.875 \end{equation}

(4)许用弯曲应力 $[\sigma_{F}]$ :

查图7.4得 $K_{FN1}=0.88$, $K_{FN2}=0.91$;

查表7.2得 $\sigma_{Flim1}=500MPa$, $\sigma_{Flim2}=500MPa$ 。

取安全系数 $S_{F}=1.4,$ 则

\begin{equation}[\sigma_{F}]_{1}=K_{FN1}\sigma_{Flim1}/S_{F}=0.88\times 500/1.4=314MPa \end{equation}

\begin{equation}[\sigma_{F}]_{2}=K_{FN2}\sigma_{Flim2}/S_{F}=0.91\times 500/1.4=325MPa \end{equation}

(5)校核:

小齿轮

\begin{equation} \begin{aligned} \sigma_{F1} &= \frac{2KT_{1}Y_{\beta}\cos^{2}\beta}{\phi_{d}\epsilon_{a}z_{1}^{2}m_{n}^{3}}Y_{Fa1}Y_{Sa1} \\ &= \frac{2\times 1.85\times 380170\times 0.875\times \cos^{2}\beta}{1\times 1.63\times 24^{2}\times 3^{3}}\times 2.57\times 1.60=186.27 \le [\sigma_{F}]_{1} \end{aligned} \end{equation}

大齿轮

\begin{equation} \begin{aligned} \sigma_{F2} &= \frac{2KT_{2}Y_{\beta}\cos^{2}\beta}{\phi_{d}\epsilon_{a}z_{2}^{2}m_{n}^{3}}Y_{Fa2}Y_{Sa2} \\ &= \frac{2\times 1.85\times 1150140\times 0.875\times \cos^{2}\beta}{1\times 1.63\times 76^{2}\times 3^{3}}\times 2.20\times 1.78=53.52 \le [\sigma_{F}]_{2} \end{aligned} \end{equation}

大小齿轮齿根弯曲疲劳强度均满足 。

由上述结果可见齿轮传动的弯曲强度有相当大的余量，故通常是按接触强度设计，确定方案后，需弯曲强度校核，这样计算比较简单。也可分别按两种强度设计，分析对比，确定方案，这样有时可以得到较优的解。

\subsubsection{齿轮传动几何尺寸计算}
(1)中心距: $a=m_{n}(z_{1}+z_{2})/(2\cos\beta)=3\times(24+76)/(2\cos 15^{\circ})=155.29mm$。 取 $a=156mm$ 。

(2)修正螺旋角: $\beta=\arccos[m_{n}(z_{1}+z_{2})/(2a)]=\arccos[3\times(24+76)/(2\times 156)]=15.59^{\circ}$ 。

(3)分度圆直径 :

\begin{equation}d_{1}=m_{n}z_{1}/\cos\beta=3\times 24/\cos 15.59^{\circ}=74.75mm \end{equation}

\begin{equation}d_{2}=m_{n}z_{2}/\cos\beta=3\times 76/\cos 15.59^{\circ}=236.72mm \end{equation}

(4)齿宽 :

\begin{equation}b=\phi_{d}d_{1}=1\times 74.75=74.75mm \end{equation}
取 $B_{2}=75mm$, $B_{1}=B_{2}+5=80mm$ 。

具体设计参数如表所示 。

\subsubsection{结果}
\begin{table}[h]
\centering
\caption{低速级齿轮}
\label{tab:gear_parameters2}
\begin{tabular}{|l|l|l|}
\hline
名称 & 代 号 & 计算公式与结果 \\ \hline
法向模数 & $m_{n}$ & 3mm \\ \hline
端面模数 & $m_{t}$ & $m_{t}=\frac{m_{n}}{\cos\beta}=3.11mm$ \\ \hline
螺旋角 & $\beta$ & $15.59^{\circ}$ \\ \hline
法向压力角 & $\alpha_{n}$ & $20^{\circ}$ \\ \hline
端面压力角 & $\alpha_{t}$ & $\alpha_{t}=\arctan(\frac{\tan\alpha_{n}}{\cos\beta})=20.71^{\circ}$ \\ \hline
分度圆直径 & $d_{1}, d_{2}$ & $74.75mm, 236.72mm$ \\ \hline
齿顶高 & $h_{a}$ & 3mm \\ \hline
齿根高 & $h_{f}$ & 3.75mm \\ \hline
全齿高 & $h$ & 6.75mm \\ \hline
顶隙 & $c$ & 0.75mm \\ \hline
齿顶圆直径 & $d_{a1}, d_{a2}$ & $80.75mm, 242.72mm$ \\ \hline
齿根圆直径 & $d_{f1}, d_{f2}$ & $67.25mm, 229.22mm$ \\ \hline
中心距 & $a$ & 156mm \\ \hline
传动比 & $i$ & 3.15 \\ \hline
齿数 & $z_{1}, z_{2}$ & 24, 76 \\ \hline
齿宽 & $b_{1}, b_{2}$ & 80mm, 75mm \\ \hline
螺旋方向 & & 小齿轮右旋, 大齿轮左旋 \\ \hline
大齿轮轮毂宽 & $B_{2}$ & 80mm \\ \hline
\end{tabular}
\end{table}

\section{轴设计}
\subsection{中间轴结构设计}

\subsubsection{选择轴材料}
选用 45 钢，调质，硬度为 230HBS。

\subsubsection{初步估算中间轴最小直径}
根据式 (9.1) 及表 9.2，取 $A=110$，则：
\begin{equation}
d \ge A\sqrt[3]{\frac{P}{n}} = 110 \times \sqrt[3]{\frac{4.9}{123.08}} = 48.36\,\mathrm{mm}
\end{equation}
因为中间轴两端弯矩和转矩均为零，也没有键槽，所以可选其最小直径 $d=55\,\mathrm{mm}$。

\subsubsection{中间轴尺寸}
考虑轴的结构及轴的刚度，取装滚动轴承处轴径 $d=60\,\mathrm{mm}$，根据轴的直径初选滚动轴承，选定圆锥滚子轴承。由轴径 $d=60\,\mathrm{mm}$ 选定滚动轴承 30212 正装布置。查附表 H.1 可得，滚动轴承宽度 $T^{\prime}=23.75\,\mathrm{mm}$， $B^{\prime}=22\,\mathrm{mm}$， $a^{\prime}=22.40\,\mathrm{mm}$。

由齿轮设计可知，高速级大齿轮轮毂宽 $B_{2}=55\,\mathrm{mm}$，低速级小齿轮宽 $B_{3}=80\,\mathrm{mm}$，选两齿轮端面间距 $\Delta=10\,\mathrm{mm}$，齿轮端面到箱内壁距离 $\Delta_{1}=12\,\mathrm{mm}$，滚动轴承端面到箱内壁距离 $\Delta_{2}=10\,\mathrm{mm}$，则箱内壁宽为：
\begin{equation}
b_{\text{内}} = B_{2} + B_{3} + \Delta + 2\Delta_{1} = 55 + 80 + 10 + 24 = 169\,\mathrm{mm}
\end{equation}

中间轴总长为：
\begin{equation}
L_{\text{中}} = b_{\text{内}} + 2\Delta_{2} + 2T^{\prime} = 169 + 20 + 47.5 = 236.5\,\mathrm{mm}
\end{equation}

% 具体结构和装配关系如图 9.18 和图 9.19 所示。

% \begin{figure}[htbp]
%   \centering
%   \framebox{\parbox{0.8\textwidth}{\centering
%     \vspace{2cm}
%     \textbf{图 9.18 / 9.19 占位符} \\
%     \small\textit{中间轴具体结构和装配关系示意图}
%     \vspace{2cm}
%   }}
%   \caption{中间轴结构与装配示意图}
% \end{figure}

\subsection{高速轴结构设计}

\subsubsection{选择轴材料}
选用 45 钢，调质，硬度为 230HBS。

\subsubsection{初步估算高速轴最小直径}
根据式 (9.1) 及表 9.2，取 $A=110$，则：
\begin{equation}
d \ge A\sqrt[3]{\frac{P}{n}} = 110 \times \sqrt[3]{\frac{5.1}{553.85}} = 23.06\,\mathrm{mm}
\end{equation}

\subsubsection{高速轴尺寸}
考虑带轮需要键槽等结构要求，以及轴的刚度，取装带轮处轴径 $d=35\,\mathrm{mm}$，取密封处的直径 $d=40\,\mathrm{mm}$，那么滚动轴承处轴径 $d=45\,\mathrm{mm}$。根据轴的直径初选滚动轴承，选定圆锥滚子轴承。由轴颈 $d=45\,\mathrm{mm}$ 选用滚动轴承 30209，正装布置。查附表 H.1 可得，滚动轴承 $T=20.75\,\mathrm{mm}$， $B=19\,\mathrm{mm}$， $a=18.60\,\mathrm{mm}$。

按滚动轴承 30209 结构，安装尺寸 $d_{a}=52\,\mathrm{mm}$。高速齿轮的齿顶圆直径 $d_1=53.82\,\mathrm{mm}$，齿根圆直径为 $d_{f1}=44.82\,\mathrm{mm}$。因此，选带退刀槽结构的齿轮轴，退刀槽直径为 44mm。

选带轮侧端面距端盖螺钉的距离为 $l_{3}=20\,\mathrm{mm}$；端盖螺钉为 M8，对应的螺钉头高度为 $k=5.3\,\mathrm{mm}$；轴承端盖厚度 $t=10\,\mathrm{mm}$；并由前面已知带轮宽度 $B_{3}=80\,\mathrm{mm}$，可得高速轴各轴段长为：

伸出段：
\begin{equation}
S = B_3 + l_3 + k + t = 80 + 20 + 5.3 + 10 = 115.3\,\mathrm{mm}
\end{equation}
圆整为 $116\,\mathrm{mm}$，即取 $l_{3}=20.7\,\mathrm{mm}$。

取滚动轴承端面到箱内壁的距离 $\Delta_{2}=10\,\mathrm{mm}$，则另一未伸出端在箱体凸缘内的长度为：
\begin{equation}
l_{4} = T + \Delta_{2} = 20.75 + 10 = 30.75\,\mathrm{mm}
\end{equation}

高速轴总长为：
\begin{equation}
L_{\text{高}} = S + h_1 + b_{\text{内}} + l_{4} = 116 + 55 + 169 + 30.75 = 370.75\,\mathrm{mm}
\end{equation}

% 高速轴的结构和装配关系见图 9.20 和图 9.21。

% \begin{figure}[htbp]
%   \centering
%   \framebox{\parbox{0.8\textwidth}{\centering
%     \vspace{2cm}
%     \textbf{图 9.20 / 9.21 占位符} \\
%     \small\textit{高速轴结构和装配关系示意图}
%     \vspace{2cm}
%   }}
%   \caption{高速轴结构与装配示意图}
% \end{figure}

\subsection{低速轴结构设计}
\subsubsection{选择轴材料}
选用 45 钢，调质，硬度为 230HBS。

\subsubsection{初步估算低速轴最小直径}
根据式 (9.1) 及表 9.2，取 $A=110$，则：
\begin{equation}
d \ge A\sqrt[3]{\frac{P}{n}} = 110 \times \sqrt[3]{\frac{4.71}{39.07}} = 54.34\,\mathrm{mm}
\end{equation}

\subsubsection{低速轴尺寸}
考虑联轴器孔径$d1=65mm$，取长度略短于半联轴器长度$l1=140mm$。
 
为满足半联轴器轴向定位，设计轴肩，第二段直径$d2=70mm$。

由于受到径向力和轴向力，应装配角接触球轴承。选择30215型轴承，轴径$d = 75 mm$，宽度$B = 25mm$因此$d3=d7=75mm$。

取挡油环宽度$s3=22mm$，则$l3=B+s3+2=25+22+2=49mm$。
 
轴承挡油环应进行轴向固定，应设置定位轴肩
 因此，取$d6=80mm$。
 
取安装齿轮处的轴的直径$d4=80mm$。已知低速级大齿轮齿宽$b=80mm$，取该段轴长$l4=78mm$。

齿轮左端采用轴肩固定，取$d5=90mm$，$l5=10mm$。

取轴承端盖厚度$e=10mm$。为了便于轴承端盖拆卸，端盖外端面距外部传动部件$K=24mm$。
\begin{equation}
l2=L+e+K-B-s=57+10+24-25-10=58mm
\end{equation}
低速级大齿轮到箱体内壁距离$\Delta=10mm$，两齿轮端面间距c=10mm，轴承距内壁s=10mm，则
\begin{equation}
l7=B+s+\Delta_2+2=25+10+10+2=47mm
\end{equation}
\begin{equation}
l6=b2+c+Δ2+s+3-l5-s1=56+10+12+10+3-10-22=57mm
\end{equation}

% 高速轴的结构和装配关系见图 9.20 和图 9.21。

% \begin{figure}[htbp]
%   \centering
%   \framebox{\parbox{0.8\textwidth}{\centering
%     \vspace{2cm}
%     \textbf{图 9.20 / 9.21 占位符} \\
%     \small\textit{高速轴结构和装配关系示意图}
%     \vspace{2cm}
%   }}
%   \caption{高速轴结构与装配示意图}
% \end{figure}

\subsection{轴强度校核}

\subsubsection{中间轴强度校核：按弯扭合成}

首先计算作用在轴上的力和力矩。

\textbf{大齿轮受力：}
\begin{itemize}
    \item 圆周力 $F_{t2} = F_{t1} = \frac{2T_{I}}{d_{1}} = 3531.5\,\mathrm{N}$
    \item 径向力 $F_{r2} = F_{r1} = \frac{F_{t1}\tan{\alpha_{n1}}}{\cos{\beta_1}} = 1334.1\,\mathrm{N}$
    \item 轴向力 $F_{a2} = F_{a1} = F_{t1}\tan{\beta_1} = 981.4\,\mathrm{N}$
\end{itemize}

\textbf{小齿轮受力：}
\begin{itemize}
    \item 圆周力 $F_{t3} = \frac{2T_{II}}{d_{3}} = 10171.8\,\mathrm{N}$
    \item 径向力 $F_{r3} = \frac{F_{t3}\tan{\alpha_{n3}}}{\cos{\beta_3}} = 3843.6\,\mathrm{N}$
    \item 轴向力 $F_{a3} = F_{t3} \tan \beta_3 = 2838.1\,\mathrm{N}$
\end{itemize}

然后校核中间轴的强度。

\paragraph{水平平面支反力：}
\[ R_{AH} = 2233\,\mathrm{N}, \quad R_{DH} = 276.5\,\mathrm{N} \]

\paragraph{垂直平面支反力：}
\[ R_{AV} = 7797.7\,\mathrm{N}, \quad R_{DV} = 5909.6\,\mathrm{N} \]

\paragraph{水平平面弯矩：}
\[ M_{BH} = -138446\,\mathrm{N \cdot mm}, \quad M_{CH} = -13624.5\,\mathrm{N \cdot mm} \]

\paragraph{垂直平面弯矩：}
\[ M_{BV1} = -483457.4\,\mathrm{N \cdot mm}, \quad M_{BV2} = -695605.375\,\mathrm{N \cdot mm} \]
\[ M_{CV1} = -291602.373\,\mathrm{N \cdot mm}, \quad M_{CV2} = -511612.625\,\mathrm{N \cdot mm} \]

\paragraph{合成弯矩：}
\[ M_{B1} = 502890\,\mathrm{N \cdot mm}, \quad M_{B2} = 695738.8\,\mathrm{N \cdot mm} \]
\[ M_{C1} = 322799.07\,\mathrm{N \cdot mm}, \quad M_{C2} = 511794\,\mathrm{N \cdot mm} \]

\paragraph{扭矩：}
\[ T = 380170\,\mathrm{N \cdot mm} \]

\paragraph{计算弯矩：}
\[ M_{caB1} = 552203.7\,\mathrm{N \cdot mm}, \quad M_{caB2} = 732176.9\,\mathrm{N \cdot mm} \]
\[ M_{caC1} = 395259.1\,\mathrm{N \cdot mm}, \quad M_{caC2} = 560324.6\,\mathrm{N \cdot mm} \]

\paragraph{绘制弯矩、扭矩图：}
\begin{figure}[h!] 
    \centering 
    
    \caption{中间轴}
    \label{fig:中间轴}
\end{figure}

\paragraph{危险截面应力校核：}
轴材料为 45 钢，经调质处理，$[\sigma_{-1}] = 60\mathrm{MPa}$。B剖面弯矩最大，$d_{B}=67.25\,\mathrm{mm}$；C剖面直径偏小，$d_{C}=65\,\mathrm{mm}$，弯矩次大。则有：

\[ \sigma_{caB} = \frac{M_{caB}}{W} = \frac{732176.9}{0.1 \times 67.25^{3}} = 24.07\,\mathrm{MPa} < [\sigma_{-1}] \]

又有：
\[ \sigma_{caC} = \frac{M_{caC}}{W} = \frac{560324.6}{0.1 \times 65^{3}} = 20.4\,\mathrm{MPa} < [\sigma_{-1}] \]

故安全，最大应力出现在弯矩最大的直径较大处。

% \subsubsection{按精确法校核轴的疲劳强度}

% \subsubsection{1) 弯矩及弯曲应力。}
% 近似认为 II-II 截面处的弯矩等于两侧弯矩峰值的平均值，即：
% \begin{equation}
% M = \frac{1\,140\,575.59 + 744\,084.96}{2} = 942\,330.27\,\mathrm{N \cdot mm}
% \end{equation}

% 抗弯剖面模量为 0.1，则：
% \[ W \approx 0.1d^{3} = 0.1 \times 65^{3} = 27\,462.50\,\mathrm{mm}^{3} \]

% 弯曲应力：
% \[ \sigma_{b} = \frac{M}{W} = 34.31\,\mathrm{MPa} \]

% 因为弯曲应力为对称循环，因此其应力幅：
% \[ \sigma_{a} = \sigma_{b} = 34.31\,\mathrm{MPa} \]

% 平均应力：
% \[ \sigma_{m} = 0\,\mathrm{MPa} \]

% \subsubsection{2) 转矩及扭转应力。}
% 转矩：
% \[ T = T_{II} = 811\,440\,\mathrm{N \cdot mm} \]

% 抗扭剖面模量：
% \[ W_{T} \approx 0.2d^{3} = 0.2 \times 65^{3} = 54\,925\,\mathrm{mm}^{3} \]

% 扭转剪应力：
% \[ \tau_{T} = \frac{T}{W_{T}} = 14.77\,\mathrm{MPa} \]

% 因为扭转应力为脉动循环，因此其应力的均值和幅值为：
% \[ \tau_{a} = \tau_{m} = \frac{1}{2}\tau_{T} = 7.39\,\mathrm{MPa} \]
% (注：原文计算结果为 9.39MPa 可能有误，此处按 $14.77/2 = 7.385$ 修正显示，后续计算沿用修正后数值或保持逻辑一致性。根据后文 $S_\tau$ 计算中代入的数值 $3.80 \times 7.39$，推断此处应为 7.39 MPa)。

% \subsubsection{3) 各项系数。}
% 过盈配合处的有效应力集中系数由教材或设计手册中查得。查表 2.2 可求得过盈配合 H7/r6。由图 2.5 和图 2.6 查得尺寸系数 $\epsilon_{\sigma}=0.70, \epsilon_{\tau}=0.70$。表面质量系数，精车加工 $\beta_{\sigma}=\beta_{\tau}=0.88$。轴未经表面强化处理，故强化系数 $\beta_{q}=1$。

% 弯曲疲劳极限的综合影响系数为：
% \[ K_{\sigma} = \left(\frac{k_{\sigma}}{\epsilon_{\sigma}} + \frac{1}{\beta_{\sigma}} - 1\right)\frac{1}{\beta_{q}} = 3.66 + \frac{1}{0.88} - 1 = 3.80 \]

% 扭转疲劳极限的综合影响系数为：
% \[ K_{\tau} = \left(\frac{k_{\tau}}{\epsilon_{\tau}} + \frac{1}{\beta_{\tau}} - 1\right)\frac{1}{\beta_{q}} = 3.66 + \frac{1}{0.88} - 1 = 3.80 \]
% (注：此处数值沿用原文，假设 $k_\sigma/\epsilon_\sigma$ 计算结果约为 3.66)。

% 材料特性系数，对碳钢 $\psi_{\sigma}=0.1 \sim 0.2$，取 $\psi_{\sigma}=0.1, \psi_{\tau}=0.05$。

% \subsubsection{4) 计算安全系数。}
% 按式 (2.13) 得：
% \begin{equation}
% S_{\sigma} = \frac{\sigma_{-1}}{K_{\sigma}\sigma_{a} + \psi_{\sigma}\sigma_{m}} = \frac{300}{3.80 \times 34.31 + 0.1 \times 0} = 2.30
% \end{equation}

% \begin{equation}
% S_{\tau} = \frac{\tau_{-1}}{K_{\tau}\tau_{a} + \psi_{\tau}\tau_{m}} = \frac{155}{3.80 \times 7.39 + 0.05 \times 7.39} = 5.45
% \end{equation}

% \begin{equation}
% S_{ca} = \frac{S_{\sigma}S_{\tau}}{\sqrt{S_{\sigma}^{2} + S_{\tau}^{2}}} = \frac{2.30 \times 5.45}{\sqrt{2.30^{2} + 5.45^{2}}} = 2.12 > S = 1.5
% \end{equation}

% \textbf{答：} 安全。

% 其他剖面计算方法与剖面 II-II 相类似，计算过程从略，结果安全。可见精确校核计算表明：轴的疲劳强度是足够的。

\subsubsection{中间轴轴承校核}
\paragraph{轴上径向、轴向载荷分析}
由轴向力 $F_{a2} = 981.4\,\text{N}$ 和 $F_{a3} = 2838.1\,\text{N}$ 得
\begin{equation}
    F_a = F_{a3} - F_{a2} = 1856.7\,\text{N}
\end{equation}
由 $R_{AH} = 2233\,\text{N}, R_{AV} = 7797.7\,\text{N}$ 得
\begin{equation}
    R_A = \sqrt{{R_{AH}}^2 + {R_{AV}}^2} = \sqrt{2233^2 + 7797.7^2} = 8111.1\,\text{N}
\end{equation}
由 $R_{DH} = 276.5\,\text{N}, R_{DV} = 5909.6\,\text{N}$ 得
\begin{equation}
    R_D = \sqrt{{R_{DH}}^2 + {R_{DV}}^2} = \sqrt{276.5^2 + 5909.6^2} = 5916.1\,\text{N}
\end{equation}
中间轴受力如图
\begin{figure}[h!] 
    \centering 
    
    
    \caption{中间轴轴承}
    \label{fig:中间轴轴承}
\end{figure}

\paragraph{轴承选型与安装}
选用代号为 \textbf{30212} 的圆锥滚子轴承，采用正装安装方式。轴承参数如下：\\
内径 $d=60\,\text{mm}$，外径 $D=110\,\text{mm}, T=23.75\,\text{mm}, B=22\,\text{mm},  a=22.4\,\text{mm}, e=0.4, Y=1.5, C_r=97.8\,\text{kN}, C_{or}=74.5\,\text{kN}$。

\paragraph{轴承内部轴向力与轴承载荷计算}
计算派生轴向力
\begin{equation}
    S_A = \frac{R_A}{2Y} = 2703.7\,\text{N}, \quad S_D = \frac{R_D}{2Y} = 1972\,\text{N}
\end{equation}
因为 $S_A + F_a > S_D$，所以
\begin{equation}
    A_A = S_A = 2703.7\,\text{N}, \quad A_D = S_A + F_a = 3828.7\,\text{N}
\end{equation}

\paragraph{轴承当量载荷计算}
因为 $\frac{A_A}{R_A} = 0.313 < e = 0.4, X_A = 1, Y_A = 0$; $\frac{A_D}{R_D} = 0.65 > e = 0.4, X_D = 0.4, Y_D = 1.5$，则
\begin{equation}
    \begin{aligned}
        P_A &= X_A R_A + Y_A A_A = 8111.1\,\text{N} \\
        P_D &= X_D R_D + Y_D A_D = 8109.5\,\text{N}
    \end{aligned}
\end{equation}

\paragraph{轴承寿命校核}
由于 $P_A > P_D$，按轴承 A 验算寿命
\begin{equation}
    L_h = \frac{10^6}{60n} \left(\frac{C}{P_A}\right)^{10/3} = \frac{10^6}{60 \times 123.08} \left(\frac{97800}{8111.1}\right)^{10/3} = 544325\,\text{h} > 15000\,\text{h}
\end{equation}
因此初选的轴承 \textbf{30212} 满足使用寿命的要求。

\subsubsection{高速轴强度校核：按弯扭合成}

首先计算作用在轴上的力和力矩。

\textbf{小齿轮受力：}
\begin{itemize}
    \item 圆周力 $F_{t1} = \frac{2T_{I}}{d_{1}} = 3531.5\,\mathrm{N}$
    \item 径向力 $F_{r1} = \frac{F_{t1}\tan{\alpha_{n1}}}{\cos{\beta_1}} = 1334.1\,\mathrm{N}$
    \item 轴向力 $F_{a1} = F_{t1}\tan{\beta_1} = 981.4\,\mathrm{N}$
\end{itemize}

然后校核中间轴的强度。

\paragraph{水平平面支反力：}
\[ R_{AH} = 349.4\,\mathrm{N}, \quad R_{DH} = 984.7\,\mathrm{N} \]

\paragraph{垂直平面支反力：}
\[ R_{AV} = -1183.6\,\mathrm{N}, \quad R_{DV} = -2347.9\,\mathrm{N} \]

\paragraph{水平平面弯矩：}
\[ M_{CH} = 48741.3\,\mathrm{N \cdot mm} \]

\paragraph{垂直平面弯矩：}
\[ M_{CV1} = 165112.2\,\mathrm{N \cdot mm}, \quad M_{CV2} = 116221.05\,\mathrm{N \cdot mm} \]

\paragraph{合成弯矩：}
\[ M_{C1} = 172156.2\,\mathrm{N \cdot mm}, \quad M_{C2} = 126028\,\mathrm{N \cdot mm} \]

\paragraph{扭矩：}
\[ T = 87970\,\mathrm{N \cdot mm} \]

\paragraph{计算弯矩：}
\[ M_{caC1} = 180065.8\,\mathrm{N \cdot mm}, \quad M_{caC2} = 136634.5\,\mathrm{N \cdot mm} \]

\paragraph{绘制弯矩、扭矩图：}
\begin{figure}[h!] 
    \centering 
    
    
    \caption{高速轴}
    \label{fig:高速轴}
\end{figure}

\paragraph{危险截面应力校核：}
轴材料为 45 钢，经调质处理，$[\sigma_{-1}] = 60\mathrm{MPa}$。C剖面弯矩最大，$d_{C}=44.82\,\mathrm{mm}$，则有：

\[ \sigma_{caC} = \frac{M_{caC}}{W} = \frac{180065.8}{0.1 \times 44.82^{3}} = 20\,\mathrm{MPa} < [\sigma_{-1}] \]

故安全。

% \subsubsection{按精确法校核轴的疲劳强度}

% 由图 9.23 中的弯矩图和转矩图可知，受载最大的剖面为 B 和 C。虽然剖面 B 上的计算弯矩最大，但该处的直径较大，且无显著的应力集中。从应力集中对轴的疲劳强度的影响来看，剖面 C、II-II 处直径较小，且过盈配合引起的应力集中在 II-II 处最严重，且该处弯矩大于 C 处，因此只对剖面 II-II 的疲劳强度进行精确校核。

% \subsubsection{1) 弯矩及弯曲应力。}
% 近似认为 II-II 截面处的弯矩等于两侧弯矩峰值的平均值，即：
% \begin{equation}
% M = \frac{1\,140\,575.59 + 744\,084.96}{2} = 942\,330.27\,\mathrm{N \cdot mm}
% \end{equation}

% 抗弯剖面模量为 0.1，则：
% \[ W \approx 0.1d^{3} = 0.1 \times 65^{3} = 27\,462.50\,\mathrm{mm}^{3} \]

% 弯曲应力：
% \[ \sigma_{b} = \frac{M}{W} = 34.31\,\mathrm{MPa} \]

% 因为弯曲应力为对称循环，因此其应力幅：
% \[ \sigma_{a} = \sigma_{b} = 34.31\,\mathrm{MPa} \]

% 平均应力：
% \[ \sigma_{m} = 0\,\mathrm{MPa} \]

% \subsubsection{2) 转矩及扭转应力。}
% 转矩：
% \[ T = T_{II} = 811\,440\,\mathrm{N \cdot mm} \]

% 抗扭剖面模量：
% \[ W_{T} \approx 0.2d^{3} = 0.2 \times 65^{3} = 54\,925\,\mathrm{mm}^{3} \]

% 扭转剪应力：
% \[ \tau_{T} = \frac{T}{W_{T}} = 14.77\,\mathrm{MPa} \]

% 因为扭转应力为脉动循环，因此其应力的均值和幅值为：
% \[ \tau_{a} = \tau_{m} = \frac{1}{2}\tau_{T} = 7.39\,\mathrm{MPa} \]
% (注：原文计算结果为 9.39MPa 可能有误，此处按 $14.77/2 = 7.385$ 修正显示，后续计算沿用修正后数值或保持逻辑一致性。根据后文 $S_\tau$ 计算中代入的数值 $3.80 \times 7.39$，推断此处应为 7.39 MPa)。

% \subsubsection{3) 各项系数。}
% 过盈配合处的有效应力集中系数由教材或设计手册中查得。查表 2.2 可求得过盈配合 H7/r6。由图 2.5 和图 2.6 查得尺寸系数 $\epsilon_{\sigma}=0.70, \epsilon_{\tau}=0.70$。表面质量系数，精车加工 $\beta_{\sigma}=\beta_{\tau}=0.88$。轴未经表面强化处理，故强化系数 $\beta_{q}=1$。

% 弯曲疲劳极限的综合影响系数为：
% \[ K_{\sigma} = \left(\frac{k_{\sigma}}{\epsilon_{\sigma}} + \frac{1}{\beta_{\sigma}} - 1\right)\frac{1}{\beta_{q}} = 3.66 + \frac{1}{0.88} - 1 = 3.80 \]

% 扭转疲劳极限的综合影响系数为：
% \[ K_{\tau} = \left(\frac{k_{\tau}}{\epsilon_{\tau}} + \frac{1}{\beta_{\tau}} - 1\right)\frac{1}{\beta_{q}} = 3.66 + \frac{1}{0.88} - 1 = 3.80 \]
% (注：此处数值沿用原文，假设 $k_\sigma/\epsilon_\sigma$ 计算结果约为 3.66)。

% 材料特性系数，对碳钢 $\psi_{\sigma}=0.1 \sim 0.2$，取 $\psi_{\sigma}=0.1, \psi_{\tau}=0.05$。

% \subsubsection{4) 计算安全系数。}
% 按式 (2.13) 得：
% \begin{equation}
% S_{\sigma} = \frac{\sigma_{-1}}{K_{\sigma}\sigma_{a} + \psi_{\sigma}\sigma_{m}} = \frac{300}{3.80 \times 34.31 + 0.1 \times 0} = 2.30
% \end{equation}

% \begin{equation}
% S_{\tau} = \frac{\tau_{-1}}{K_{\tau}\tau_{a} + \psi_{\tau}\tau_{m}} = \frac{155}{3.80 \times 7.39 + 0.05 \times 7.39} = 5.45
% \end{equation}

% \begin{equation}
% S_{ca} = \frac{S_{\sigma}S_{\tau}}{\sqrt{S_{\sigma}^{2} + S_{\tau}^{2}}} = \frac{2.30 \times 5.45}{\sqrt{2.30^{2} + 5.45^{2}}} = 2.12 > S = 1.5
% \end{equation}

% \textbf{答：} 安全。

% 其他剖面计算方法与剖面 II-II 相类似，计算过程从略，结果安全。可见精确校核计算表明：轴的疲劳强度是足够的。

\subsubsection{高速轴轴承校核}
\paragraph{轴上径向、轴向载荷分析}
由轴向力 $F_{a1} = 981.4\,\text{N}$得
\begin{equation}
    F_a = F_{a1} = 981.4\,\text{N}
\end{equation}
由 $R_{AH} = 349.4\,\text{N}, R_{AV} = 1183.6\,\text{N}$ 得
\begin{equation}
    R_A = \sqrt{{R_{AH}}^2 + {R_{AV}}^2} = \sqrt{349.4^2 + 1183.6^2} = 1234.1\,\text{N}
\end{equation}
由 $R_{DH} = 984.7\,\text{N}, R_{DV} = 2347.9\,\text{N}$ 得
\begin{equation}
    R_D = \sqrt{{R_{DH}}^2 + {R_{DV}}^2} = \sqrt{984.7^2 + 2347.9^2} = 2546\,\text{N}
\end{equation}
中间轴受力如图
\begin{figure}[h!] 
    \centering 
    
    
    \caption{高速轴轴承}
    \label{fig:高速轴轴承}
\end{figure}

\paragraph{轴承选型与安装}
选用代号为 \textbf{30209} 的圆锥滚子轴承，采用正装安装方式。轴承参数如下：\\
内径 $d=45\,\text{mm}$，外径 $D=85\,\text{mm}, T=20.75\,\text{mm}, B=19\,\text{mm},  a=18.6\,\text{mm}, e=0.4, Y=1.5, C_r=64.2\,\text{kN}, C_{or}=47.8\,\text{kN}$。

\paragraph{轴承内部轴向力与轴承载荷计算}
计算派生轴向力
\begin{equation}
    S_A = \frac{R_A}{2Y} = 411.4\,\text{N}, \quad S_D = \frac{R_D}{2Y} = 848.7\,\text{N}
\end{equation}
因为 $S_A + F_a > S_D$，所以
\begin{equation}
    A_A = S_A = 411.4\,\text{N}, \quad A_D = S_A + F_a = 1392.8\,\text{N}
\end{equation}

\paragraph{轴承当量载荷计算}
因为 $\frac{A_A}{R_A} = 0.33 < e = 0.4, X_A = 1, Y_A = 0$; $\frac{A_D}{R_D} = 0.55 > e = 0.4, X_D = 0.4, Y_D = 1.5$，则
\begin{equation}
    \begin{aligned}
        P_A &= X_A R_A + Y_A A_A = 1234.1\,\text{N} \\
        P_D &= X_D R_D + Y_D A_D = 3107.6\,\text{N}
    \end{aligned}
\end{equation}

\paragraph{轴承寿命校核}
由于 $P_A < P_D$，按轴承 D 验算寿命
\begin{equation}
    L_h = \frac{10^6}{60n} \left(\frac{C}{P_D}\right)^{10/3} = \frac{10^6}{60 \times 553.85} \left(\frac{64200}{3107.6}\right)^{10/3} = 728042\,\text{h} > 15000\,\text{h}
\end{equation}
因此初选的轴承 \textbf{30209} 满足使用寿命的要求。

\subsubsection{低速轴强度校核：按弯扭合成}

首先计算作用在轴上的力和力矩。

\textbf{大齿轮受力：}
\begin{itemize}
    \item 圆周力 $F_{t4} = F_{t3} = \frac{2T_{II}}{d_{3}} = 10171.8\,\mathrm{N}$
    \item 径向力 $F_{r4} = F_{r3} = \frac{F_{t3}\tan{\alpha_{n3}}}{\cos{\beta_3}} = 3843.6\,\mathrm{N}$
    \item 轴向力 $F_{a4} = F_{t4} \tan \beta_3 = 2838.1\,\mathrm{N}$
\end{itemize}

然后校核中间轴的强度。

\paragraph{水平平面支反力：}
\[ R_{AH} = 2569.2\,\mathrm{N}, \quad R_{DH} = 1274.4\,\mathrm{N} \]

\paragraph{垂直平面支反力：}
\[ R_{AV} = -3235.1\,\mathrm{N}, \quad R_{DV} = -6936.7\,\mathrm{N} \]

\paragraph{水平平面弯矩：}
\[ M_{CH} = 160575\,\mathrm{N \cdot mm} \]

\paragraph{垂直平面弯矩：}
\[ M_{BV1} = 202193.75\,\mathrm{N \cdot mm}, \quad M_{BV2} = 874024.2\,\mathrm{N \cdot mm} \]

\paragraph{合成弯矩：}
\[ M_{B1} = 258198.8\,\mathrm{N \cdot mm}, \quad M_{B2} = 888652.1\,\mathrm{N \cdot mm} \]

\paragraph{扭矩：}
\[ T = 1150140\,\mathrm{N \cdot mm} \]

\paragraph{计算弯矩：}
\[ M_{caB1} = 736805.6\,\mathrm{N \cdot mm}, \quad M_{caB2} = 1125130\,\mathrm{N \cdot mm} \]

\paragraph{绘制弯矩、扭矩图：}
\begin{figure}[h!] 
    \centering 
    
    
    \caption{低速轴}
    \label{fig:低速轴}
\end{figure}

\paragraph{危险截面应力校核：}
轴材料为 45 钢，经调质处理，$[\sigma_{-1}] = 60\mathrm{MPa}$。B剖面弯矩最大，$d_{B}=80\,\mathrm{mm}$，则有：

\[ \sigma_{caB} = \frac{M_{caB}}{W} = \frac{1125130}{0.1 \times 80^{3}} = 21.98\,\mathrm{MPa} < [\sigma_{-1}] \]

故安全。

% \subsubsection{按精确法校核轴的疲劳强度}

% 由图 9.23 中的弯矩图和转矩图可知，受载最大的剖面为 B 和 C。虽然剖面 B 上的计算弯矩最大，但该处的直径较大，且无显著的应力集中。从应力集中对轴的疲劳强度的影响来看，剖面 C、II-II 处直径较小，且过盈配合引起的应力集中在 II-II 处最严重，且该处弯矩大于 C 处，因此只对剖面 II-II 的疲劳强度进行精确校核。

% \subsubsection{1) 弯矩及弯曲应力。}
% 近似认为 II-II 截面处的弯矩等于两侧弯矩峰值的平均值，即：
% \begin{equation}
% M = \frac{1\,140\,575.59 + 744\,084.96}{2} = 942\,330.27\,\mathrm{N \cdot mm}
% \end{equation}

% 抗弯剖面模量为 0.1，则：
% \[ W \approx 0.1d^{3} = 0.1 \times 65^{3} = 27\,462.50\,\mathrm{mm}^{3} \]

% 弯曲应力：
% \[ \sigma_{b} = \frac{M}{W} = 34.31\,\mathrm{MPa} \]

% 因为弯曲应力为对称循环，因此其应力幅：
% \[ \sigma_{a} = \sigma_{b} = 34.31\,\mathrm{MPa} \]

% 平均应力：
% \[ \sigma_{m} = 0\,\mathrm{MPa} \]

% \subsubsection{2) 转矩及扭转应力。}
% 转矩：
% \[ T = T_{II} = 811\,440\,\mathrm{N \cdot mm} \]

% 抗扭剖面模量：
% \[ W_{T} \approx 0.2d^{3} = 0.2 \times 65^{3} = 54\,925\,\mathrm{mm}^{3} \]

% 扭转剪应力：
% \[ \tau_{T} = \frac{T}{W_{T}} = 14.77\,\mathrm{MPa} \]

% 因为扭转应力为脉动循环，因此其应力的均值和幅值为：
% \[ \tau_{a} = \tau_{m} = \frac{1}{2}\tau_{T} = 7.39\,\mathrm{MPa} \]
% (注：原文计算结果为 9.39MPa 可能有误，此处按 $14.77/2 = 7.385$ 修正显示，后续计算沿用修正后数值或保持逻辑一致性。根据后文 $S_\tau$ 计算中代入的数值 $3.80 \times 7.39$，推断此处应为 7.39 MPa)。

% \subsubsection{3) 各项系数。}
% 过盈配合处的有效应力集中系数由教材或设计手册中查得。查表 2.2 可求得过盈配合 H7/r6。由图 2.5 和图 2.6 查得尺寸系数 $\epsilon_{\sigma}=0.70, \epsilon_{\tau}=0.70$。表面质量系数，精车加工 $\beta_{\sigma}=\beta_{\tau}=0.88$。轴未经表面强化处理，故强化系数 $\beta_{q}=1$。

% 弯曲疲劳极限的综合影响系数为：
% \[ K_{\sigma} = \left(\frac{k_{\sigma}}{\epsilon_{\sigma}} + \frac{1}{\beta_{\sigma}} - 1\right)\frac{1}{\beta_{q}} = 3.66 + \frac{1}{0.88} - 1 = 3.80 \]

% 扭转疲劳极限的综合影响系数为：
% \[ K_{\tau} = \left(\frac{k_{\tau}}{\epsilon_{\tau}} + \frac{1}{\beta_{\tau}} - 1\right)\frac{1}{\beta_{q}} = 3.66 + \frac{1}{0.88} - 1 = 3.80 \]
% (注：此处数值沿用原文，假设 $k_\sigma/\epsilon_\sigma$ 计算结果约为 3.66)。

% 材料特性系数，对碳钢 $\psi_{\sigma}=0.1 \sim 0.2$，取 $\psi_{\sigma}=0.1, \psi_{\tau}=0.05$。

% \subsubsection{4) 计算安全系数。}
% 按式 (2.13) 得：
% \begin{equation}
% S_{\sigma} = \frac{\sigma_{-1}}{K_{\sigma}\sigma_{a} + \psi_{\sigma}\sigma_{m}} = \frac{300}{3.80 \times 34.31 + 0.1 \times 0} = 2.30
% \end{equation}

% \begin{equation}
% S_{\tau} = \frac{\tau_{-1}}{K_{\tau}\tau_{a} + \psi_{\tau}\tau_{m}} = \frac{155}{3.80 \times 7.39 + 0.05 \times 7.39} = 5.45
% \end{equation}

% \begin{equation}
% S_{ca} = \frac{S_{\sigma}S_{\tau}}{\sqrt{S_{\sigma}^{2} + S_{\tau}^{2}}} = \frac{2.30 \times 5.45}{\sqrt{2.30^{2} + 5.45^{2}}} = 2.12 > S = 1.5
% \end{equation}

% \textbf{答：} 安全。

% 其他剖面计算方法与剖面 II-II 相类似，计算过程从略，结果安全。可见精确校核计算表明：轴的疲劳强度是足够的。

\subsubsection{低速轴轴承校核}
\paragraph{轴上径向、轴向载荷分析}
由轴向力 $F_{a4} = 3838.1 \,\text{N}$得
\begin{equation}
    F_a = F_{a4} = 3838.1\,\text{N}
\end{equation}
由 $R_{AH} = 2569.2\,\text{N}, R_{AV} = 3235.1\,\text{N}$ 得
\begin{equation}
    R_A = \sqrt{{R_{AH}}^2 + {R_{AV}}^2} = \sqrt{2569.2^2 + 3235.1^2} = 4131.2\,\text{N}
\end{equation}
由 $R_{DH} = 1274.4 \,\text{N}, R_{DV} = 6936.7\,\text{N}$ 得
\begin{equation}
    R_D = \sqrt{{R_{DH}}^2 + {R_{DV}}^2} = \sqrt{1274.4^2 + 6936.7^2} = 7052.7\,\text{N}
\end{equation}
中间轴受力如图
\begin{figure}[h!] 
    \centering 
    
    
    \caption{低速轴轴承}
    \label{fig:低速轴轴承}
\end{figure}

\paragraph{轴承选型与安装}% 改轴承，尺寸
选用代号为 \textbf{30215} 的圆锥滚子轴承，采用正装安装方式。轴承参数如下：\\
内径 $d=75\,\text{mm}$，外径 $D=130\,\text{mm}, T = 27.25\,\text{mm}, \,\text{mm}, B=25\,\text{mm},  a=27.4\,\text{mm}, e=0.44, Y=1.4, C_r=130\,\text{kN}, C_{or}=105\,\text{kN}$。

\paragraph{轴承内部轴向力与轴承载荷计算}
计算派生轴向力
\begin{equation}
    S_A = \frac{R_A}{2Y} = 1475.4\,\text{N}, \quad S_D = \frac{R_D}{2Y} = 2518.8\,\text{N}
\end{equation}
因为 $S_A + F_a > S_D$，所以
\begin{equation}
    A_A = S_A = 1475.4\,\text{N}, \quad A_D = S_A + F_a = 5313.5\,\text{N}
\end{equation}

\paragraph{轴承当量载荷计算}
因为 $\frac{A_A}{R_A} = 0.36 < e = 0.44, X_A = 1, Y_A = 0$; $\frac{A_D}{R_D} = 0.75 > e = 0.4, X_D = 0.4, Y_D = 1.4$，则
\begin{equation}
    \begin{aligned}
        P_A &= X_A R_A + Y_A A_A = 4131.2\,\text{N} \\
        P_D &= X_D R_D + Y_D A_D = 10260\,\text{N}
    \end{aligned}
\end{equation}

\paragraph{轴承寿命校核}
由于 $P_A < P_D$，按轴承 D 验算寿命
\begin{equation}
    L_h = \frac{10^6}{60n} \left(\frac{C}{P_A}\right)^{10/3} = \frac{10^6}{60 \times 39.07} \left(\frac{130000}{10260}\right)^{10/3} = 2022980\,\text{h} > 15000\,\text{h}
\end{equation}
因此初选的轴承 \textbf{30215} 满足使用寿命的要求。

\section{键设计}
\subsection{高速轴与大带轮间轴}

\begin{enumerate}
    \item[(1)] \textbf{选择键的类型} \quad 因蜗轮工作时对中性要求较高，故选 A 型普通平键
    \item[(2)] \textbf{确定键的尺寸} \quad 根据题意，由附录E查得：键宽 $b=10\text{mm}$，键高 $h=8\text{mm}$，键长 $L=70\text{mm}$
    \item[(3)] \textbf{校核挤压强度} \quad 许用挤压应力 $[\sigma_p] = 110\text{MPa}$
\end{enumerate}

\subsubsection{转矩}
\begin{equation}
    T = 9.55 \times 10^6 P/n = 9.55 \times 10^6 \times \frac{5.1015}{553.85} = 87970 \text{ N} \cdot \text{mm}
\end{equation}

\subsubsection{键工作长度}
\begin{equation}
    l = L - b = (70 - 10) \, \text{mm} = 60 \, \text{mm}
\end{equation}

\subsubsection{键与键槽的工作高度}
\begin{equation}
    k = h/2 = 8/2 \, \text{mm} = 4 \, \text{mm}
\end{equation}

\subsubsection{挤压应力} 
\begin{equation}
\begin{aligned}
    \sigma_p &= \frac{2T}{kld} = \frac{2 \times 87970}{4 \times 60 \times 35} \, \text{MPa} \\
             &= 20.9 \, \text{MPa} < [\sigma_p]\, \text{MPa}
\end{aligned}
\end{equation}

结论：键连接满足强度条件

\subsection{中间轴与大齿轮间轴}
\begin{enumerate}
    \item[(1)] \textbf{选择键的类型} \quad 因蜗轮工作时对中性要求较高，故选 A 型普通平键
    \item[(2)] \textbf{确定键的尺寸} \quad 根据题意，由附录E查得：键宽 $b=20\text{mm}$，键高 $h=12\text{mm}$，键长 $L=40\text{mm}$
    \item[(3)] \textbf{校核挤压强度} \quad 许用挤压应力 $[\sigma_p] = 110\text{MPa}$
\end{enumerate}

\subsubsection{转矩}
\begin{equation}
    T = 9.55 \times 10^6 P/n = 9.55 \times 10^6 \times \frac{4.8995}{123.08} = 380170 \text{ N} \cdot \text{mm}
\end{equation}

\subsubsection{键工作长度}
\begin{equation}
    l = L - b = (40 - 20) \, \text{mm} = 20 \, \text{mm}
\end{equation}

\subsubsection{键与键槽的工作高度}
\begin{equation}
    k = h/2 = 12/2 \, \text{mm} = 6 \, \text{mm}
\end{equation}

\subsubsection{挤压应力} 
\begin{equation}
\begin{aligned}
    \sigma_p &= \frac{2T}{kld} = \frac{2 \times 380170}{6 \times 20 \times 65} \, \text{MPa} \\
             &= 97.5 \, \text{MPa} < [\sigma_p]\, \text{MPa}
\end{aligned}
\end{equation}

结论：键连接满足强度条件

\subsection{低速轴与大齿轮间轴}
\begin{enumerate}
    \item[(1)] \textbf{选择键的类型} \quad 因蜗轮工作时对中性要求较高，故选 A 型普通平键
    \item[(2)] \textbf{确定键的尺寸} \quad 根据题意，由附录E查得：键宽 $b=22\text{mm}$，键高 $h=14\text{mm}$，键长 $L=70\text{mm}$
    \item[(3)] \textbf{校核挤压强度} \quad 许用挤压应力 $[\sigma_p] = 110\text{MPa}$
\end{enumerate}

\subsubsection{转矩}
\begin{equation}
    T = 9.55 \times 10^6 P/n = 9.55 \times 10^6 \times \frac{4.7055}{39.07} = 1150140 \text{ N} \cdot \text{mm}
\end{equation}

\subsubsection{键工作长度}
\begin{equation}
    l = L - b = (70 - 22) \, \text{mm} = 48 \, \text{mm}
\end{equation}

\subsubsection{键与键槽的工作高度}
\begin{equation}
    k = h/2 = 14/2 \, \text{mm} = 7 \, \text{mm}
\end{equation}

\subsubsection{挤压应力} 
\begin{equation}
\begin{aligned}
    \sigma_p &= \frac{2T}{kld} = \frac{2 \times 1150140}{7 \times 48 \times 80} \, \text{MPa} \\
             &= 85.6 \, \text{MPa} < [\sigma_p]\, \text{MPa}
\end{aligned}
\end{equation}

结论：键连接满足强度条件

\subsection{低速轴与联轴器间轴}
\begin{enumerate}
    \item[(1)] \textbf{选择键的类型} \quad 因蜗轮工作时对中性要求较高，故选 A 型普通平键
    \item[(2)] \textbf{确定键的尺寸} \quad 根据题意，由附录E查得：键宽 $b=20\text{mm}$，键高 $h=12\text{mm}$，键长 $L=125\text{mm}$
    \item[(3)] \textbf{校核挤压强度} \quad 许用挤压应力 $[\sigma_p] = 110\text{MPa}$
\end{enumerate}

\subsubsection{转矩}
\begin{equation}
    T = 9.55 \times 10^6 P/n = 9.55 \times 10^6 \times \frac{4.7055}{39.07} = 1150140 \text{ N} \cdot \text{mm}
\end{equation}

\subsubsection{键工作长度}
\begin{equation}
    l = L - b = (125 - 20) \, \text{mm} = 105 \, \text{mm}
\end{equation}

\subsubsection{键与键槽的工作高度}
\begin{equation}
    k = h/2 = 12/2 \, \text{mm} = 6 \, \text{mm}
\end{equation}

\subsubsection{挤压应力} 
\begin{equation}
\begin{aligned}
    \sigma_p &= \frac{2T}{kld} = \frac{2 \times 1150140}{6 \times 105 \times 65} \, \text{MPa} \\
             &= 56.2 \, \text{MPa} < [\sigma_p]
\end{aligned}
\end{equation}

结论：键连接满足强度条件

\section{联轴器选择}
\subsection{高速轴上联轴器}
由表查得载荷系数$K_A=1.3$，计算转矩$T_C=K_A\times T=1.3×87.97=114.36\text{ N} \cdot \text{mm}$

轴伸出端安装的联轴器初选为 LX3 联轴器，其公称转矩 $T_n=1250 \, \mathrm{N \cdot m}$，许用转速 $[n]=4750 \, \mathrm{r/min}$，采用 Y 型轴孔。其中主动端孔直径 $d=35 \, \mathrm{mm}$，轴孔长度 $L=82 \, \mathrm{mm}$；从动端孔直径 $d=30 \, \mathrm{mm}$，轴孔长度 $L=82 \, \mathrm{mm}$。

验算如下：
\begin{align*}
    T_c &= 114.36 \, \mathrm{N \cdot m} < T_n \\
    n &= 553.85 \, \mathrm{r/min} < [n]
\end{align*}
满足要求。

\subsection{低速轴上联轴器}
由表查得载荷系数$K_A=1.3$，计算转矩$T_C=K_A\times T=1.3×1150.14=1495.182\text{ N} \cdot \text{mm}$

轴伸出端安装的联轴器初选为 LX6 联轴器，其公称转矩 $T_n=6300 \, \mathrm{N \cdot m}$，许用转速 $[n]=2720 \, \mathrm{r/min}$，采用 Y 型轴孔。其中主动端孔直径 $d=65 \, \mathrm{mm}$，轴孔长度 $L=142 \, \mathrm{mm}$；从动端孔直径 $d=60 \, \mathrm{mm}$，轴孔长度 $L=142 \, \mathrm{mm}$。

验算如下：
\begin{align*}
    T_c &= 1495.18 \, \mathrm{N \cdot m} < T_n \\
    n &= 39.07 \, \mathrm{r/min} < [n]
\end{align*}
满足要求。

\section{润滑}
\subsection{齿轮的润滑}
为了避免减速器工作时大齿轮搅起油池底面的沉积物，又要保证箱座有
足够的容积存放传动所需的润滑油，由于齿轮的速度：
\begin{equation}
    v = \frac{\pi d_1 n}{60\times1000}=\frac{\pi\times63.53\times553.85}{60\times1000} = 1.84 \text{m/s}<12 \text{m/s}
\end{equation}
故齿轮采用油池浸油润滑，选用 L-CKC150润滑 油，大齿轮浸油深度约为 15mm。

\subsection{轴承的润滑}
由于齿轮圆周速度$v<2 \text{m/s}$，故轴承的润滑方式采用润滑脂润滑，选用 4号钙基润滑脂。

\section{窥视孔及窥视孔盖}
窥视孔用于检查传动件的啮合情况、润滑状态、接触斑点及齿侧间隙，还可用于注入润滑油，故窥视孔应开在便于观察齿轮啮合区的位置，其尺寸大小应便于检查。窥视孔盖可以用铸铁、钢板制成，它和箱体之间应加密封垫。

\begin{figure}[h!] 
    \centering 
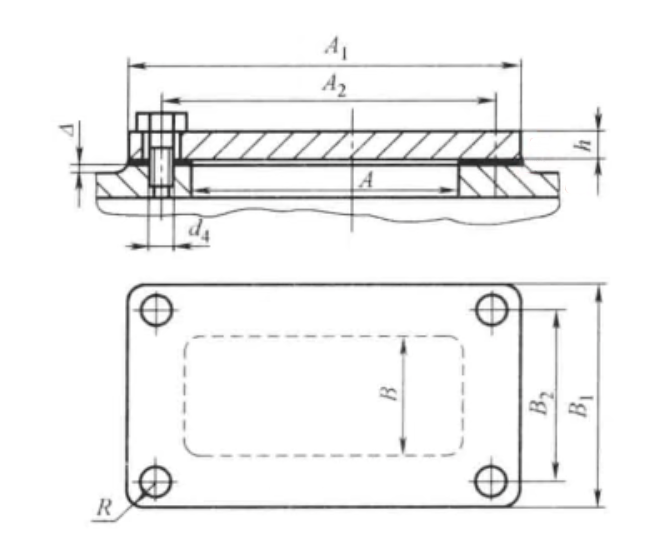
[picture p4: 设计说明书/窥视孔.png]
    
    \caption{窥视孔及窥视孔盖}
    \label{fig:窥视孔及窥视孔盖}
\end{figure}

\section{放油孔及放油螺塞}
为排放减速器箱体内污油和便于清洗箱体内部，在箱座油池的最低处设置放油孔，箱体内底面做成斜面，向放油孔方向倾斜1°～2°，使油易于流出。选择$d = 24$的放油螺塞。

\begin{figure}[h!] 
    \centering 
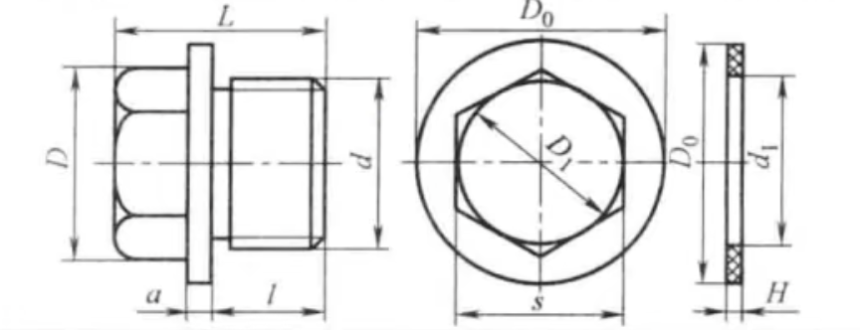
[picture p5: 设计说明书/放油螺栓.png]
    
    \caption{放油螺塞}
    \label{fig:放油螺塞}
\end{figure}

\section{油尺}
油尺用来指示油面高度，应设置在便于检查及油面较稳定之处。本设计采用杆式油标，杆式油标结构简单，其上有刻线表示最高及最低油面。油标安置的位置不能太低，以防油溢出。其倾斜角度应便于油标座孔的加工及油标的装拆。

\begin{figure}[h!] 
    \centering 
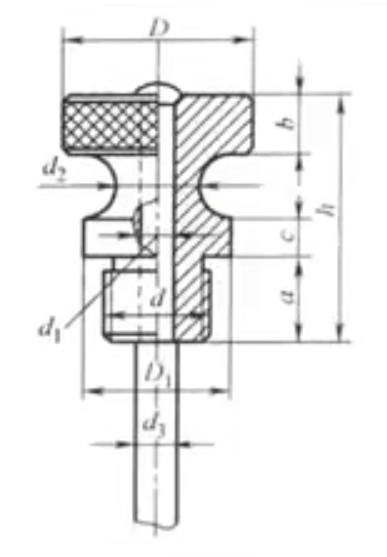
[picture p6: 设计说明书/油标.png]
    
    \caption{油尺}
    \label{fig:油尺}
\end{figure}

\section{通气器}
通气器用于通气，使箱体内外气压一致，以免由于运转时箱体内温度升高，内压增大，而引起减速器润滑油的渗漏。简易的通气器钻有丁字形孔，常设置在箱顶或检查孔盖上，用于较清洁的环境。较完善的通气器具有过滤网及通气曲路，可减少灰尘进入。

\begin{figure}[h!] 
    \centering 
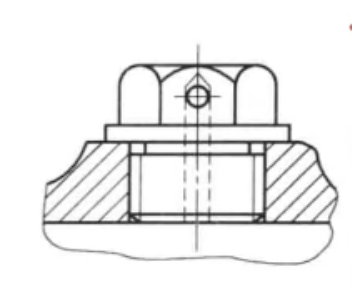
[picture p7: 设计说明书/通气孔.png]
    
    \caption{通气孔}
    \label{fig:通气孔}
\end{figure}

\section{起吊装置}
起吊装置用于拆卸及搬运减速器。它常由箱盖上的吊孔和箱座凸缘下面的吊耳构成。也可采用吊环螺钉拧入箱盖以吊小型减速器或吊起箱盖。本设计中所采用吊孔（或吊环）和吊耳的示例和尺寸如下图所示：起吊装置用于拆卸及搬运减速器。

\begin{figure}[h!] 
    \centering 
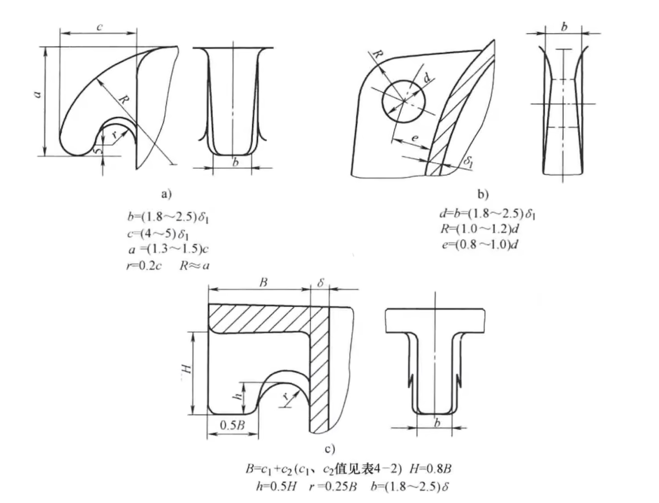
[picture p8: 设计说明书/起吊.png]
    
    \caption{起吊装置}
    \label{fig:起吊装置}
\end{figure}

\section{起盖螺钉}
为便于起箱盖，可在箱盖凸缘上装设2个起盖螺钉。拆卸箱盖时，可先拧动此螺钉顶起箱盖。起盖螺钉头部应为圆柱形，以免损坏螺纹。选择M10的起盖螺钉。

\section{定位销}
为保证箱体轴承孔的加工精度与装配精度，应在箱体链接凸缘上相距较远处安置两个圆锥销，并尽量放在不对称位置，以使箱座与箱盖能正确定位。为便于拆装，定位销长度应大于链接凸缘总厚度。

\begin{figure}[h!] 
    \centering 
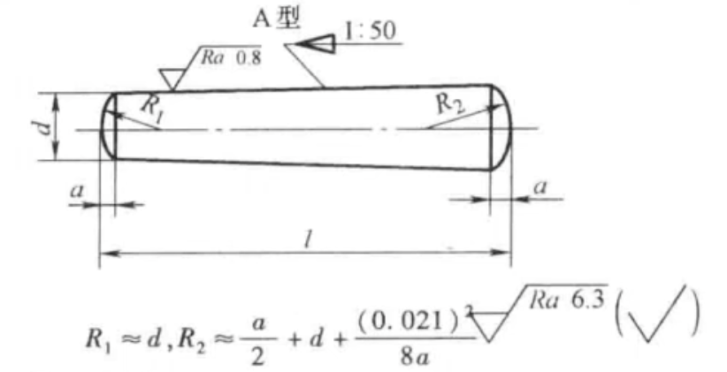
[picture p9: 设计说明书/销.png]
    
    \caption{定位销}
    \label{fig:定位销}
\end{figure}

\section{设计小结}
通过这门机械设计课程的学习，我系统掌握了二级展开式圆柱齿轮减速箱的设计与分析方法，收获显著。在亲身参与设计项目过程中，我不仅巩固了相关理论知识，也提升了实践能力与问题解决能力。

首先，课程使我对机械设计的整体流程有了更为清晰的把握。从需求分析到测试验证，每个阶段都需要严谨的思考和精确的计算，使我深切感受到设计的复杂性与挑战性。尤其在齿轮选型、强度计算等环节，我学会了如何运用工程原理解决实际问题，这显著增强了我的专业素养。

其次，课程的实践环节进一步加深了我对理论知识的理解。通过实际设计与应用相结合的过程，我更加明确了理论指导实践的重要性，也坚定了今后从事机械工程相关工作的信心。

总之，本课程使我对机械设计的各个环节形成了较为全面的认识。我期待在今后的学习与工作中运用所学的知识与技能，持续探索这一富有创造性的领域。

\section{参考文献}
黄平——《机械设计教程——理论、方法与标准（第二版）》清华大学出版社

\end{document}

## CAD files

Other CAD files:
零件图(中间轴).dwg
装配图.dwg

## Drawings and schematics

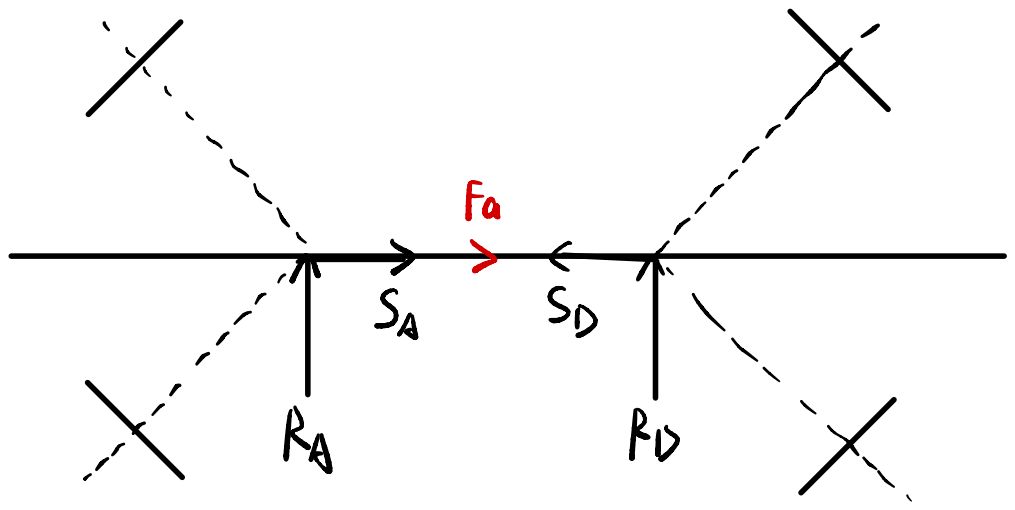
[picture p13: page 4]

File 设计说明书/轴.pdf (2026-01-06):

点 | !
,

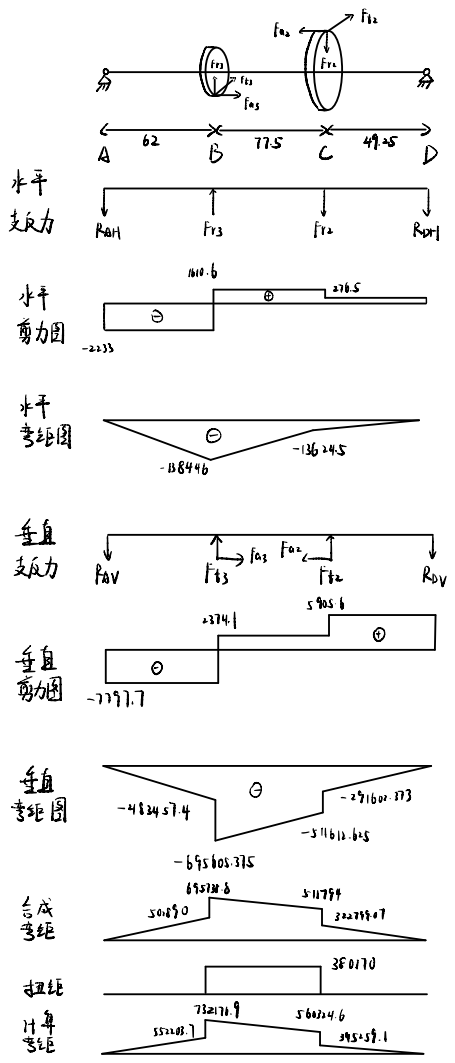
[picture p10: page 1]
> iic; kAH; irs; 剪力图品 θ; 弯距图; 反力阳v; → 的昆Fac

步 | ( pim | ,,

## Fil (

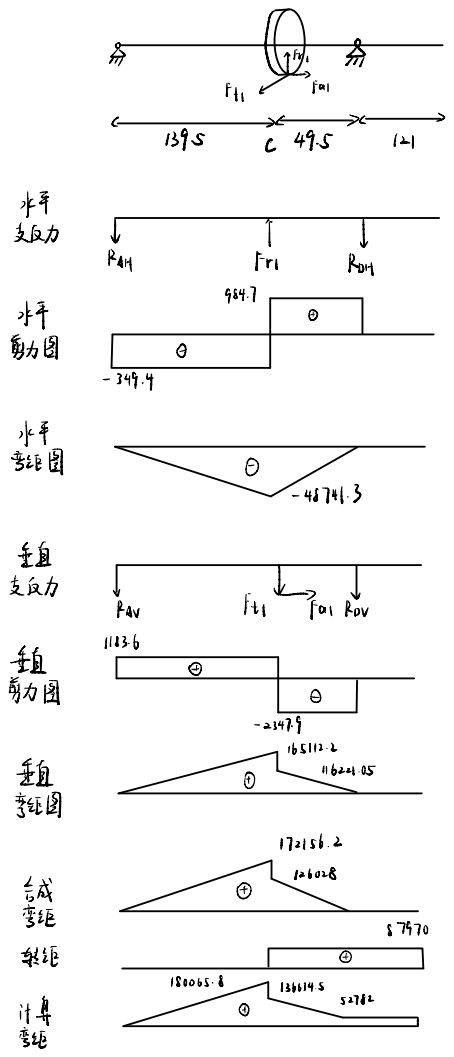
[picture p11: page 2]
Fas; 交级力; PimRpry; 剪力图; 弯钜图

Ya , Ror 产荒 ④

## Fuy Σ

炅 (

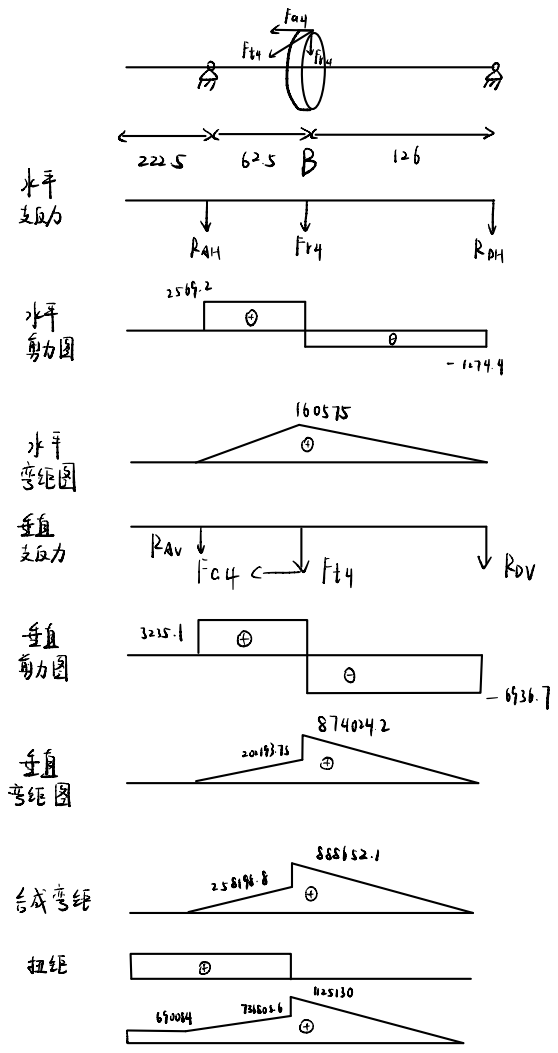
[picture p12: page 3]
PAHFry; 剪力图; 弯钜图; 志反力; RAr d; Fty; V RpV; 言成弯距; 6SuV3G

## 管品 “公RiB '
